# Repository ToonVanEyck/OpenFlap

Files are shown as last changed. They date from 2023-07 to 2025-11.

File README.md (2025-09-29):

# OpenFlap




!!! warning

    🚨 This is still a work in progress. Using the the code and files in this repository to create your own display is not recommended at the moment! 🚨

The OpenFlap project aims to create a open source, affordable split-flap display for the makers and tinkerers of the world.
This repository houses all the required files to build, program and modify your very own split-flap display. 

[**Read the Docs**](https://toonvaneyck.github.io/OpenFlap/)

OpenFlap Module

## Specifications

- 48 Flaps per module.
- 49mm x 70mm Character size.
- Stackable & Chainable.
- Daisy chain communication.
- Per module configuration & calibration.
- HTTP API available.
- Modular design.
- 3D printable parts.

## Design Philosophy

The OpenFlap system is designed to be modular and expandable, using common components and manufacturing techniques such as 3D printing and printed circuit boards.

The OpenFlap system uses DC geared motors instead of traditional stepper motors. This simplifies the mechanical design and reduces the cost of the system. Additionally this reduces the power consumption of the system and allows the split-flap display to rotate faster than the traditionally used stepper motors. 

The OpenFlap system is designed to be as plug and play as possible. The system is able to determine it's own display size, and should only require calibration once.

The OpenFlap system has a web interface that allows local control of the display. The web interface uses a HTTP API to communicate with the display, this API also allows external services to communicate with the display. No authentication or security measures are implemented at the moment.

The OpenFlap system can connect to your local WiFi network or host it's own network.

## I want to ...

[... know more about how the OpenFlap system works.](docs/architecture.md)

[... build my own OpenFlap display.](todo)

[... contribute to the OpenFlap project.](docs/developing.md)

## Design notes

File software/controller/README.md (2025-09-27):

# Controller firmware development with ESP-IDF

To get started, make sure you have build and opened the `esp-idf` devcontainer in VS-Code.

!!! info
    
    All commands below are to be run from the root of the repository.

!!! note

    You may set the `OPENFLAP_DEFAULT_SSID` and `OPENFLAP_DEFAULT_PASSWORD` environment variables to override the default WiFi SSID and password for the controller. If not set, the controller will default to `default_ssid` and `default_password`.

## Build the firmware

```bash
idf.py -B build/controller -C software/controller build
```

## Flash the firmware

```bash
idf.py -B build/controller -C software/controller flash monitor
```

!!! note 

    The first time you program the controller, you will need to use the UART0 RX/TX pads on the bottom of the board. After the initial programming, you can use the USB port to program and debug the controller.+

## Action Buttons

The VS Code devcontainer contains a toolbar with some useful actions for building and flashing the firmware.

ESP-IDF Action Buttons

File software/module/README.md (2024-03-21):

# Puya Playground

This is a VS-Code devcontainer based development environment for the Puya PY32 family of ARM Cortex M0 microcontrollers. It's based on [IOsetting's work](https://github.com/IOsetting/py32f0-template) but it has been wrapped in a devcontainer and I changed the build system to CMake.

I have tested this setup with [this devkit from aliexpress](https://nl.aliexpress.com/item/1005004959178538.html).

## Getting Started

Connect the devkit as shown in the image below.

devkit

Start the development container

In the development container verify that the debug probe is connected:
```
vscode ➜ /workspace/build $ pyocd list
  #   Probe/Board             Unique ID                                          Target         
------------------------------------------------------------------------------------------------
  0   ARM DAPLink CMSIS-DAP   070000003233d72f083932363836374da5a5a5a597969908   ✖︎ stm32f103rb  
      NUCLEO-F103RB
```

## Building
```
mkdir build
cd build
cmake -DCMAKE_TOOLCHAIN_FILE=puya_toolchain.cmake ..
make
make flash
```

## Debugging
A `launch.json` file is configured to use the debug capabilities of VS-Code

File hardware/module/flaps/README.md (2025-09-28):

# Flaps

This repository contains two methods to create the flaps for the OpenFlap split flap display.
Either you can order them as 0.8mm PCB's or you can 3D print them using a multicolor printer.

## Flap Generator

The Flap generator is a browser based tool which allows you to quickly generate a character set for the OpenFlap display. You can select a font, size and the desired character set. Additionally you can adjust the scale, width and position of each character. The tool allows you to export and import your project file so you can continue your work at a later time.

A default character set is contained within the `defaultFlapSet.json` file. This file is loaded by default within the application. The default file contains the following character set:

```text
 ABCDEFGHIJKLMNOPQRSTUVWXYZ0123456789€$!?.,:/@#&
```

By clicking on the **Generate Files** button, a set of *.svg* files are generated for each flap. Each flap contains a top and bottom layer. The top layer contain the upper part of the character and the bottom layer contains the lower part of the next character flipped vertically. All files are bundled in a *.zip* and downloaded to your computer. The *.svg* files within this *.zip* folder are meant to be used by [gerbolyze](https://github.com/jaseg/gerbolyze) to generate the gerber files for the production of the flaps.

A wrapper script `flaps_to_pcb.sh` is provide witch takes two inputs: the input *.zip* file generated by the browser based flap generator and the output directory where the gerber files will be stored. The script will extract the *.zip* file and run `gerbolyze` on each *.svg* file. The output gerber files will be stored as a *.zip* file in the output directory. 

In a similar way, the script `flaps_to_3d.py` takes the same input *.zip* file and generates a set of *.stl* files for each flap. The output *.stl* files are stored in the output directory.

Click the link to use the [Flap Generator](browser_based_flap_generator/index.html).

## Considerations

When creating a character set, make sure the flaps do not have any part of the character show below a certain distance from the bottom. This is because the bottom of previous flaps are always visible on the display. In the OpenFlap display, it's around 5mm from the bottom of the flap. The default character set uses 8mm to be on the safe side.

## ToDo

- Add support for custom svg glyph upload.

## Known Issues

- It's possible that "holes" in svg paths are "closed" when increasing the thickness of a glyph. This will only become apparent when viewing the gerbers as it does not show up in the generator tool.

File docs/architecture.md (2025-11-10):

# Architecture

The OpenFlap system can be divided into 3 main components:

- The [**OpenFlap Module**](module.md)
- The [**OpenFlap Top Connector**](top_connector.md)
- The [**OpenFlap Controller**](controller.md)

To build an OpenFlap display, you need one OpenFlap Controller for the first column of modules, a Top Connector for all other columns of modules, and some OpenFlap Modules.

This chapter describes how these 3 components works and communicate.

## Display Size restrictions

There are two factors that limit the maximum size of the display:

### 1. The power required to drive all the modules.

The lowest rated connection allows for a maximum current of 15A. At 12V this means that the maximum power that can be delivered to the display is 180W. Each module draws around 1W while moving. This limits the maximum 'safe' display size to around 180 modules. As the modules do not rotate all the time, it is possible to drive larger displays, but this has not been tested.

### 2. The memory required by the controller to keep track of all the modules.

The controller keeps an internal representation of the display in memory. The maximum number of modules which can be controlled a the same time without running out of memory is untested at the moment.

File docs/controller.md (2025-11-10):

# OpenFlap Controller

The controller is a special kind of Top Connector. It is meant to be used for the first column of modules in the display. It's based around the espresif ESP32-S3, a low-cost, microcontroller with integrated WiFi and Bluetooth capabilities. 
The controller is responsible for managing and communicating with the modules over UART, as well presenting a web interface and API to the user. 

OpenFlap Controller Render

The controller must be powered from a 12V power supply using the XT-30 connector. A USB port is provided for programming and debugging.

## Additional Resources

- [Schematic](../hardware/controller/controller-schematic.pdf)
- [Interactive BOM](../hardware/controller/controller-ibom.html)
- [KiCanvas](https://kicanvas.org/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)

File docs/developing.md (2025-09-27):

# Developing

This repository contains everything you need to build and develop the OpenFlap display system. To effectively develop and contribute to the project, it's important that you are familiar with the following technologies:

- VS-Code devcontainers
- ESP-IDF & FreeRTOS
- ARM Bare Metal development
- KiCad & FreeCAD

## Devcontainers 

All firmware development for this project is done using VS-Code devcontainers. The repository contains the following devcontainers:

### 1) esp-idf

This development container is set up for developing the controller firmware. It contains the ESP-IDF framework and all the required tools to build and flash the firmware to the controller.

### 2) puya 

This development container is set up for developing the module firmware. It contains the ARM toolchain and all the required tools to build and flash the firmware to the module.

### 3) ecad-mcad

This development container is used for automating the generation of PCB production files and 3D printing files. It contains KiCad, FreeCAD and all the required tools to generate the production files. Actual development of the PCB's and 3D models is done outside of the devcontainer.

## Repository Structure

This repository contains everything you need to build and develop the OpenFlap display system. The repository is structured as follows:

- `.devcontainer`: Contains the devcontainer definitions for the 3 development containers.
- `docs`: Contains the documentation for the project.
- `hardware`: Contains all the hardware (PCB) designs for the project.
- `software`: Contains all the software for the project.
- `mechanical`: Contains all the mechanical designs for the project.

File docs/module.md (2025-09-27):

# OpenFlap Module

The OpenFlap module is the main component of the OpenFlap system. It consists of number of 3D prints and PCBs sandwiched together to create a display.

OpenFlap Module CAD model

The construction of the module can be described as follows:
A 3D printed 'shell' is sandwiched between two side panel PCBs. A 3D printed bearing is mounted on each of the side panels and the 'flap wheel' is mounted on these bearings. The flap wheel consists of 3D printed core sandwiched between two PCBs. All the flaps rest between these two PCBs. 

Only the left side panel PCB is populated with components. The right side panel PCB is left unpopulated and is used to provide mechanical support. 

!!! note

    In theory, the unpopulated side panel PCB could be replaced with a 3D printed part, this 3D printed part could then also be fused with the 'shell' and on of the 'bearings' greatly simplifying the assembly process and reducing the part count. But it would make the design asymmetrical and I just won't have it...

## Side Panel PCB

Two side panels make up the main structure of the module. The left side panel is populated with components and the right side panel is left unpopulated. The side panel PCB is responsible for the following tasks:

- **Motor Control**: The side panel PCB is responsible for controlling the motor that drives the flaps.
- **Communication**: The side panel PCB is responsible for communicating with the controller and the other modules over UART.
- **Flap Detection**: The side panel PCB is responsible for detecting the position of the flaps.

Each left side panel features a [Puya PY32F003F1](https://download.py32.org/ReferenceManual/en/PY32F003%20Reference%20manual%20v1.1_EN.pdf), this is a low cost 32 bit ARM cortex M0+ microcontroller. 

Three [ITR8307](https://www.everlighteurope.com/custom/files/datasheets/DRX-0000321.pdf) reflective optical sensors are used to detect the position of the flaps. They do this by detecting an [incremental encoder](https://en.wikipedia.org/wiki/Incremental_encoder) pattern on the flap wheel. 

The motor is driven by a [L9110S](https://www.lcsc.com/datasheet/lcsc_datasheet_2203301130_LANKE-L9110S_C2984833.pdf) motor driver. PWM is used to modulate the speed of the motor. 

2x7 Pin headers sit at the top and bottom of the PCB to connect the side panel to the other modules. One pin in the bottom header is always pulled low by the next module below it. When the module is the last in the chain, this pin is pulled high by a pull-up resistor. This way the module can determine if it is the last in a column.

OpenFlap Side Panel Render

!!! note

    There is a dependency between the encoder pattern and the position of the IR sensors. The encoder pattern is designed with 48 flaps in mind, this determines the IR sensors placement. If you want to change the number of flaps, you will have to change the encoder pattern and the position of the IR sensors.

### Additional Resources

- [Schematic](../hardware/module/side_panel/side_panel-schematic.pdf)
- [Interactive BOM](../hardware/module/side_panel/side_panel-ibom.html)
- [KiCanvas](https://kicanvas.org/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)

## Encoder Wheels PCB

Two encoder wheel PCB sandwiches the 3D printed "core" of the module. The encoder wheels holds all the flaps and allows the the side panel to track it's rotation.

Each encoder wheel has an A & B side. On the A side, the encoder pattern is offset 4.5° relative to the flap holes. On the B side this offset is 3.75°. This allows you tho switch the side in case the flaps are rotating to far / not far enough.

OpenFlap Encoder Wheels Render

## Flaps

Initially the flaps were designed to be PCB's. But due to the increased accessibility of multicolor 3D printers, the flaps can now also be 3D printed. 

A software tool to generate a custom flap set is included in this repository. As well as script to generate the gerber files or STL files for the flaps. ( TODO: Add link to the tool )

Flap Dimensions

## Shell 

The shell is designed to be 3D printed. Its features include:

- **Mounting holes**: The shell has mounting holes for the side panel PCBs and the top connector.
- **Flap retainer**: The flap retainer, retains the upper flap without covering it up entirely. 
- **Dovetails**: The shell has 2 dovetail cutouts on the back, allowing for flexible mounting options.
- **Ratchet notch**: A notch on the inside of the shell prevents the flap wheel from spinning in the wrong direction.

Openflap Shell Ratchet Notch

When the flap wheel spins and finally reaches its setpoint, the motor will spin in reverse for a short pulse. Because the flaps will lock up against the ratchet notch, all modules will end up at the same position height wise. Additionally, this action will take up the backlash in the gearbox, preventing the flaps from sagging.

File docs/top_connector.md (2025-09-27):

# OpenFlap Top Connector

As the name suggests, the Top Connector is placed at the top of each column of modules. The Top Connector routes power and communication signals to the modules in the column. Top Connectors can be connected together using 2x9 IDC ribbon cables, Allowing the display to be daisy chained to any* width.

OpenFlap Top Connector Render

## Functions

- Receive 12V from previous column and pass it to the next column.
- Convert 12V to 5V using a DC-DC converter and supply it to the modules in the column.
- Route UART signal from previous column through to this column and to the next column.
- Reroute UART back to previous column when this is the last column.

Top Connector Diagram

## Additional Resources

- [Schematic](../hardware/top_connector/top_connector-schematic.pdf)
- [Interactive BOM](../hardware/top_connector/top_connector-ibom.html)
- [KiCanvas](https://kicanvas.org/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)

(*) Power consumption and voltage drop over long cables may limit the practical width of the display.

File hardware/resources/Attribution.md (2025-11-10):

Source files for the 3D models used in the hardware design.
Sources may not be the original creators of the models, but the files were found on the following websites.

| File | Source |
| ---- | --- |
|[694106106102.stp (and .wrl)](694106106102.stp) | [INTI-CMNB on github](https://github.com/INTI-CMNB/kibot_variants_arduprog/tree/master/3D) |
|[DC_jack_plug_5.5x2.5.stp](DC_jack_plug_5.5x2.5.stp) | [nomura.kenzi-1 on grabcad](https://grabcad.com/library/dc-jack-plug-5-5x2-5-angle-1) |
|[EVQ-P7J01P.stp](EVQ-P7J01P.stp) | [snapeda](https://www.snapeda.com/parts/EVQ-P7J01P/Panasonic/view-part/) |
|[GA12-N20.stp](GA12-N20.stp) | [vip1990-1 on grabcad](https://grabcad.com/library/ga12-n20-motor-1) |
|[HLE-107-02-L-DV-BE-A-TR.stp](HLE-107-02-L-DV-BE-A-TR.stp) | [samtec](https://www.samtec.com/products/hle-107-02-l-dv-be-a-tr) |
|[HLE-108-02-L-DV-BE-TR.stp](HLE-108-02-L-DV-BE-TR.stp) | [samtec](https://www.samtec.com/products/hle-108-02-l-dv-be-tr) |
|[IDC_1.27mm_2x3.stp](IDC_1.27mm_2x3.stp) | [bakatrouble-1 on grabcad](https://grabcad.com/library/idc-box-header-1-27mm-1) |
|[IDC_1.27mm_2x5.stp](IDC_1.27mm_2x5.stp) | [bakatrouble-1 on grabcad](https://grabcad.com/library/idc-box-header-1-27mm-1) |
|[Right-angle-USB-C-cable.stp](Right-angle-USB-C-cable.stp) | [mike.d-83 on grabcad](https://grabcad.com/library/right-angle-usb-c-to-4-pin-bare-wire-1) |
|[USB-C.stp](USB-C.stp) | [neal.wong-1 on grabcad](https://grabcad.com/library/usb-type-c16pin-vertical-type-1) |
|[54-00286.STEP](54-00286.STEP) | [Digikey](https://www.digikey.be/en/models/16649077) |
|[WS2812-0807.stp](WS2812-0807.stp) | [ilya.kopytov-1 on grabcad](https://grabcad.com/library/ws2812-0807-1) |
|[XT30-STEP](XT30-STEP) | [stuplja-1 on grabcad](https://grabcad.com/library/xt30-male-connector-1) |

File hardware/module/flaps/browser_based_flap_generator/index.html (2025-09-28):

Project Setup

Load Project

Save Project

Font

Variant

Size

Character Set

Type the complete character set you wish to generate in here.

Show Guide Lines

Top Guide

mm

Bottom Guide

mm

Character Y Offset

mm

Generate Files

Flap Properties

Scale

Thickness

X Position

mm

Y Position

mm

# Welcome to the OpenFlap Flap Generator!

This tool allows you to generate a set of SVG files required to produce the flap PCB's.

Additionally, you can tweak each glyph's position and size.

Once the you have downloaded the ZIP file containing all SVG's, you can convert them to gerbers or stl's using the flaps_to_pcb.sh or flaps_to_3d.py utility in this repository.

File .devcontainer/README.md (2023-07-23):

# OpenFlap dev container 

## How to use the devcontainer

[tutorial](https://code.visualstudio.com/docs/devcontainers/tutorial)

- Open this directory in vscode.
- Make sure the `Dev Containers` extension is installed.
- Open the command pallet with `F1` of `Ctrl+Shif+P` and select `Dev Containers: Open Workspace In Container`.
- The devcointainer will build.

## Adding USB devices to the devcontainer

Based on [this stack overflow answer](https://stackoverflow.com/a/66427245).

Use the files in `.devcontainer/utils`.

On your host machine:
```bash
sudo cp .devcontainer/utils/99-docker-tty.rules /etc/udev/rules.d/99-docker-tty.rules
sudo service udev restart
sudo cp .devcontainer/utils/docker_tty.sh /usr/local/bin/docker_tty.sh
```

## Using git in your container

Vscode should automatically forward your git & ssh credentials if your ssh-agent is running. Otherwise [check this](https://code.visualstudio.com/remote/advancedcontainers/sharing-git-credentials).

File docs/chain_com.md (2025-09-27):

# Communication

The communication system between the controller and the modules is a daisy chain system based on UART. The controller sends a message to the first module, the first module processes the message and sends it to the next module. This continues until the last module in the chain has received the message.

## Header

There are 4 action types for message send by the controller to the modules:

| Value | Action | Description |
|---|---|---|
| 0 | read all | Read a property from all modules. |
| 1 | write sequential | Write a different value to different properties of a number of sequential modules. |
| 2 | write all | Write the same value to the property of all modules. |
| 3 | execute / return code | Signal the modules to execute a command and return a return code. |

The action type of the message is defined by the 2 most significant bits in the message header byte. The six least significant bits are used to define the property to read or write. This means that there are 64 possible properties that can be read or written. Each property has a read and a write length, this length can be either static or dynamic. In the case of a dynamic length, the length is passed in the message itself.

These are the currently supported properties:

| Value | Property | Read Size | Write Size | Description |
|---|---|---|---|---|
| 0 | NONE | 0 | 0 | Nothing |
| 1 | Firmware Version  | Dynamic | 0 | Contains the firmware version |
| 2 | Firmware Update | 0 | 130 | Used for performing a firmware update. |
| 3 | Command | 0 | 1 | Write a special command, e.g.: reboot, ... |
| 4 | Module Info | 1 | 0 | Property containing the module type and column end information. |
| 5 | Character Set | Dynamic | Dynamic | The possible characters supported by this module. |
| 6 | Character Index | 1 | 1 | The index of the character displayed in the character set. |
| 7 | Encoder Offset | 1 | 1 | The offset between the encoder 'zero' and the first character in the set. |
| 8 | Color | 2 | 2 | Flap fore- and background colors. |
| 9 | Motion | 4 | 4 | Rotational speed control. |
| 10 | Minimum rotation  | 1 | 1 | The minimum number of flaps that should be rotated when changing characters. |
| 11 | Sensor threshold  | 4 | 4 | Threshold values for the IR encoders. |

## Checksum 

The tree primary message types (read all, write all, write sequential) include some form of single byte checksum. This checksum allows the controller and modules to verify that the message was received correctly. The checksum is calculated by summing all bytes in the message (excluding the checksum byte itself) and taking the least significant byte of the result. The location and number of checksum bytes depends on the message type.

## Execute / Return Code

This is a special action type that is used to signal the modules to execute a command and return a return code. When this action is used, the 6 property bytes are used to communicate the return code. Each module will logically `OR` its return code with the return code in the header. This way the controller can determine if any module in the chain encountered an error.

## Read All 

This action is used to read a property from all modules in the chain.

The controller initiates a read all action by sending a header with the action set to `read all` followed by two counting bytes. Each module will retransmit the header, the counting bytes will be retransmitted as well, but each module will increment the counting bytes by one. Next, the module will transmit the property data, followed by a checksum. Sequential modules will know how much data from previous modules to retransmit based of the counting bytes. The last module will retransmit to the controller, which can use the counting bytes to figure out how many modules are in the chain.

Here is an example of a read all message with a property size of 2 bytes:
Property Read All Static

When a property has a dynamic read size. The module will first transmit the size of the property data (2 bytes), followed by the property data itself. Sequential modules will first read the size of the property data so they know how much data they need to retransmit.

Property Read All Dynamic

Each module append's its own checksum to the end of its data. This checksum includes the header and sum of the two counting bytes of its own index in the chain.

## Write All

This action is used to write the same property value to all modules in the chain. This is useful for applying bulk changes to all modules. E.g: Homing the display or applying a firmware update.

The controller initiates a write all action by sending a header with the action set to `write all` followed by the property data and a checksum byte. The message is terminated with an `execute / return code` header. Each module will retransmit the `write all` header and the property data. Once a module has retransmitted the property data, and determined the checksum to be valid, it will process the data and wait for the `execute / return code` header. Once it has received the header, it will logically `OR` its return code with the header. If the checksum is invalid, the module will not process the data and will return an error code instead.

Property Write All Static

When a property has a dynamic write size. The module will first transmit the size of the property data (2 bytes) before transmitting the property data itself.

Property Write All Dynamic

## Write Sequential

This action is used to write different property values to different modules in the chain.

The controller will send multiple header and data + checksum packets. Typically one for each module. The message is terminated by two sequential `execute / return code` headers. The first `execute / return code` header gets retransmitted by each module imeadiatly and triggers the processing of the received data. The second `execute / return code` header will only be retransmitted after the module has finished processing the data. The combination of these two `execute / return code` headers allow the modules to know when the controller has finished sending data, and it allows the controller to know when the modules have finished processing the data.

The `NONE` property can be used to skip a module in the chain. This can be useful when you want to write a property to a specific module in the chain.

Dynamic and static property sizes can be mixed in together in a single message. But typically the controller will stick to one property at a time.

Property Write Sequential

## Examples (Outdated, does not contain CS)

The character property is a good example to show the 3 different action types. The character property has a static read and write size of 1 byte. For this example let's assume the character property id is `5` or `0b000101`.

Our headers would look like this:

| Action | Action (bin) | Property (bin) | Header (bin) | Header (hex) |
|---|---|---|---|---|
| read_all  | 0b01000000 | 0b000101 | 0b01000101 | **0x45** |
| write_seq | 0b10000000 | 0b000101 | 0b10000101 | **0x85** |
| write_all | 0b11000000 | 0b000101 | 0b11000101 | **0xC5** |

The character property will return a number between 0 and 47. This number is the index of the character in the character set. For this example let's assume the character set starts like this `_ABCDEFGHIJKLMNOPQRSTUVWXYZ`. So when the character property is set to `0` the character displayed will be `_`, when the character property is set to `1` the character displayed will be `A`, when the character property is set to `2` the character displayed will be `B`, etc.

**We will start by reading the character property from all modules in the chain:**

Example Read All

We can see the controller transmit the read all header `0x45` followed by the counting bytes `0x00 0x00`.
We receive the header `0x45` followed by the counting bytes `0x05 0x00`, followed by 5 bytes of data. The controller can determine that there are 5 modules in the chain by looking at the counting bytes. The data `0x08 0x05 0x0C 0x0C 0x0F` corresponds to the characters `HELLO` in the character map. 

**Let's finish that message:**

We will write `WORLD` to the modules. This corresponds to the character indexes `0x17 0x0F 0x12 0x0C 0x04`. This will require some sequential write messages. We will use the header `0x85` for this.

Example Write Seq

We can see 5 header and data packets being transmitted by the controller followed by an ACK byte. On the receiving site we only see the ACK byte being received, this is because every module 'takes' one message and retransmits the remaining messages. By the message return to the controller, only the ACK remains.

**Finally we clear the display:**

We will write the character index `0x00` to all modules in the chain. We will use the header `0xC5` for this.

Example Write All

We see the header, followed by the data, followed by the ACK byte transmitted by the controller. The exact same data passes through all modules and is received by the controller.

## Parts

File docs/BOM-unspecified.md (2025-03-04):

List of miscellaneous components required for the project. This file will be cleaned up and organized later.

## Module:
- [60 RPM 12V GA12-N20 DC Gear Motor](http://aliexpress.com/item/33022320164.html)
- [3mm motor coupler](https://aliexpress.com/item/4000342135388.html)
- [M2.6 x 8mm screws](https://aliexpress.com/item/1005003094076706.html)

## Top Connector:
- [2x8 Female 2.54mm Low Profile Bottom Entry Header Socket](https://aliexpress.com/item/3256803077112247.html)
- [2x8 2.54mm idc Connector](https://aliexpress.com/item/2255801071215566.html)
- [16 PIN Ribbon Cable](https://aliexpress.com/item/2251832811689611.html)

## Controller:
- [Optional OLED Display](https://aliexpress.com/item/2251832607894397.html)
- [2x3 & 2x5 1.27mm idc Socket](https://aliexpress.com/item/3256805806476804.html)

## Programmers:
- ESP-PROG
- SWD Programmer

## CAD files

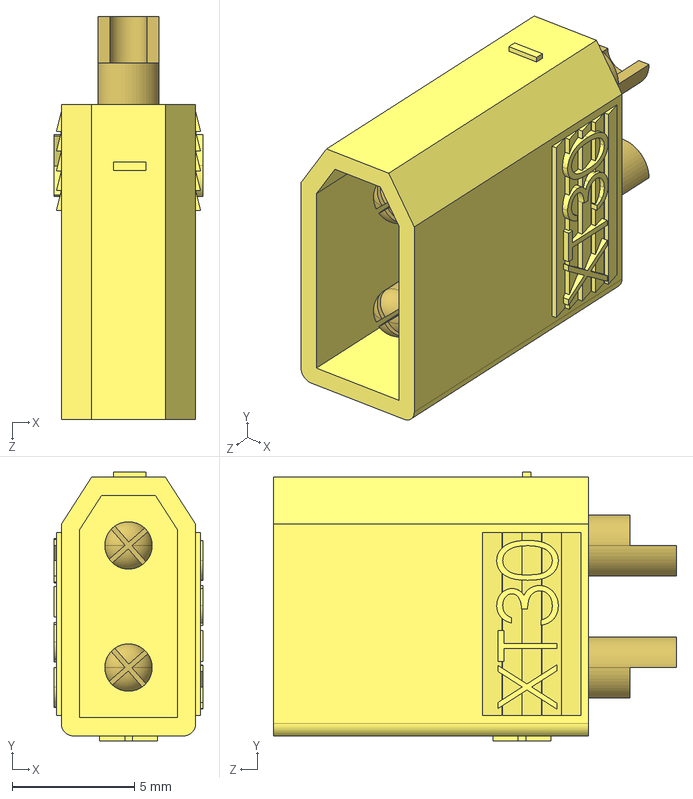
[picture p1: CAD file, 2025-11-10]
hardware/resources/XT30-M.STEP
6.10 x 11.0 x 16.5 mm

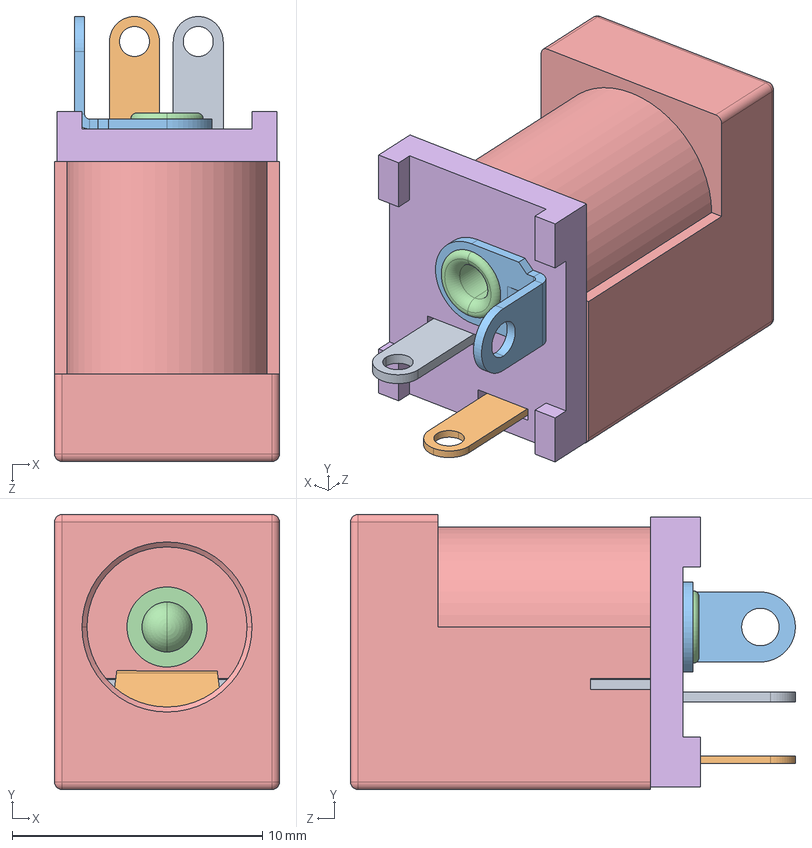
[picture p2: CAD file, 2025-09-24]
hardware/resources/54-00286.STEP
9.00 x 11.0 x 17.8 mm
54-00286_switch
54-00286_spring
54-00286_pin tab
54-00286_pin
54-00286_Insulator
54-00286_Insulator2

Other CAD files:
mechanical/openflap_cad_model.FCStd
hardware/resources/EVQ-P7J01P.stp
hardware/resources/DC_jack_plug_5.5x2.5.stp
hardware/resources/Right-angle-USB-C-cable.stp
hardware/resources/USB-C.stp
hardware/resources/WS2812-0807.stp
hardware/resources/HLE-107-02-L-DV-BE-A-TR.stp
hardware/resources/HLE-108-02-L-DV-BE-TR.stp
hardware/resources/IDC_1.27mm_2x5.stp
hardware/resources/IDC_1.27mm_2x3.stp
hardware/resources/GA12-N20.stp
hardware/resources/694106106102.stp

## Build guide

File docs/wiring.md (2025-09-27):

## Wiring, signaling and power distribution

The system is wired by connecting the top connectors together with a ribbon cable. The first top connector is connected to the OpenFlap Controller. The OpenFlap Modules can be stacked on top of each other and connected to a top connector.

The top connectors and modules a equipped with a sensor witch allows them to detect if they are connected to another module or top connector. This allows the system to determine the size of the display and simplifies the wiring process.

The image below show the signal path from the OpenFlap Controller through the OpenFlap Modules and back:

OpenFlap Signal Path

The controller can be provided with 12V DC power through a barrel jack. This 12V is passed on to the top connectors and modules through the ribbon cable. The top connectors have a voltage regulator that converts the 12V to 5V. This 5V supply is shared by all the modules connected below the top connector.

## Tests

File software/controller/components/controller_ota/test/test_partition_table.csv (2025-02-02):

# Name | Type | SubType | Offset | Size | Flags
nvs | data | nvs | 0x009000 | 16K
otadata | data | ota |  | 8K
phy_init | data | phy |  | 4K
ota_0 | app | ota_0 |  | 4M
ota_1 | app | ota_1 |  | 4M
flash_test | data | fat |  | 100K

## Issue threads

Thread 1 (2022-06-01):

Optimizing for Columns instead of Rows?

graham768, 2022-06-01:
Hey ToonVanEyck,

First of all, I love the work you've done. I think I stumbled onto this project fairly early considering the commit dates and the time stamps on your schematics, but you're really blowing the other "competition" out of the water by making these modules so compact and interchangeable.

With the interchangeability though, I was wondering why you optimized the design for columns. If I'm understanding correctly each column has to have its own top-con board, so if I made a board with 10 modules in a row I'd need 10 top-con boards? Whereas if I made a single column of 10 modules stacked tall, I'd only need a single top-con for the whole system? I would expect most users to have more modules in a row than a column as they write phrases. Let me know if I've misunderstood anything here!

ToonVanEyck, 2022-06-01:
Hey Graham,

Thanks for your intrest in the project.

Each module has two PCB side panels, only one of those PCB's (the left one) has any components on it. The other PCB is the just a structural part. When stacking the modules we can use the headers as implemented in the current design. If we would want to connect them left to right we would need to use a cable or other pcb to connect the left PCB of the first module with the left PCB of the next PCB. This seems like a more complex solution.

Additionally, I wanted the display to be easy to disassemble in the field. It's important to be able to quickly replace one broken module from anywhere in the display. The the top and bottom of the side panel PCB's are rounded. (This is done to reduces the inter-line distance of the display.) Once the modules are stacked and placed in a display, it is impossible to remove a single module or an entire row from a display. It's only possible to remove an entire column from the display, and then break apart that column to replace a broken module.

Because we already have all the connections available on the topmost modules of each column it seemed logical to add a board to facilitate wiring them together.

NOTE: It's entirely possible to wire multiple modules in a row without the use of the top-con boards. (An external 5V supply is required.) The top-con just simplify this greatly.

I agree that horizontal stacking would be more favourable for most users. But the vertical stacking and interconnection was just more practical to implement.  The top-con board allows the horizontal connections to be made with a simple flat-cable to simplify the wiring.

Closed 2022-06-01.

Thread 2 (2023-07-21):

Uploading Flaps Gerbers to JLCPCB

joelhauxwell, 2023-07-21:
Hey ToonVanEyck,

I know the project landing page for this warns against building anything just yet but i would really like to build some of your amazing modules.

I have tried to upload one of the flap gerber zips to JLCPCB but there seems to be an issue with the file.  It opens in the Gerber Preview pane with errors:

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

And in the main order page, the size isn't detected:

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

I could enter the dims manually and select the option for 'confirm production file' -  did you also have to do this?

If you think that me embarking on this project is a terrible idea then please let me know!

Thanks,

Joel.

ToonVanEyck, 2023-07-21:
Hi Joel, JLC pcb seems to have these issues when the Gerber files don't contain anything on the copper layers of the Gerbers. Please let me check if all the latest Gerbers are on GitHub. I will try to update them this weekend. I will also try to write a small manual this weekend.

ToonVanEyck, 2023-07-22:
Hi Joel,

I updated all production files as well as the README. The readme now includes all additional parts you will need as well as all the tools required.
You will also find some additional info for ordering the flaps and encoder wheels on JLCPCB in the readme.
If you have any more questions/issues, don't hesitate to ask them through GitHub issues.

Regards,
Toon

Closed 2023-07-22.

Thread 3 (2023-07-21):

Fusion 360 Links Unauthorized

joelhauxwell, 2023-07-21:
Hey ToonVanEyck,

I can't see the Encoder PCB in the production gerber files and using the Eagle link results in an error -

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

Please could you upload the production files for the encoder wheels when you get a chance?

Thanks,

Joel.

ToonVanEyck, 2023-07-22:
I have removed the links in favour of eagle .sch and .brd files

Closed 2023-07-22.

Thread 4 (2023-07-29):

Alternative for optical sensor

joelhauxwell, 2023-07-29:
Hey,

The optical sensor in the BOM is out of stock at LCSC without a date.

This looks like an appropriate alternative - https://www.lcsc.com/product-detail/Reflective-Optical-Interrupters_Everlight-Elec-ITR8307-S17-TR8-B_C81632.html

What you do think?

Thanks,

Joel.

ToonVanEyck, 2023-07-29:
Seems like it should work. It's cheaper too, so good catch!

Closed 2023-07-29.

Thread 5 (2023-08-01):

[DISCUSSION] Support for multi-width & multi-format displays

sashahilton00, 2023-08-01:
Hi,

I was wondering if there are any plans to support larger displays, both in terms of number of modules, but also in terms of modules of differing width, such as:

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

I have a few thoughts on how one might do this, and might prototype a little, but wanted to check if there is already a WIP on this front:

- Looking at the designs, I'm slightly concerned that if one connected a couple of hundred modules together, that there may be concerns around power draw, possibly necessitating a seperate header (unpopulated by default) for power on each module, which could be used instead of the power from the 16 pin connector for powering the PIC/motor.
- For the multi width side of things, the simplest way in my mind, is to say that the standard module is 1 unit wide, then allow for multiples of the standard unit to be used, to keep the grid type web UI simple, and retain the neat auto discovery functionality.
- Each unit would then store it's size (eg. unit width: 3) in the MCU, and to allow the columnar communication system to continue to work, one would have a simple bridging board that linked the modules above and below an extended width module, with a stored unit length of zero. In this way, a module that detected a module connected below it (ie. column end = false), where that module had a unit width of 0, would allow it to determine that it was sitting on top of a module with a unit length > 1, and be displayed accordingly in the UI. This would probably also require a minor modification to add a lip to the top and bottom casing that would allow modules to snap into to retain their position.

ToonVanEyck, 2023-08-02:
Hi,

Interesting!

I currently do not plan on developing wider modules. I think you are on the right track. E.g.: A 3 wide module should contain 1 PCB with microcontroller, motor, etc... Configured with a `module_width = 3`. And 2 PCBs which just pass through the data signals. These 2 passthrough PCBs should also detect if they are at the end of a column and reroute the data accordingly. I don't think they would require a `module_width = 0`, they don't require a microcontroller. The OpenFlap Controller should be able to calculate the date order in order to "skip" the passthrough PCBs.

Regarding the power usage:
I don't know the power draw at the moment, but the column height will be the limiting factor here. For multiple rows it's trivial to create a customized cable that powers different columns from different supplies. I have ordered materials to build 30 modules, this will allow me to profile the power usage of a somewhat larger display.

I also had the idea for different kinds of modules, e.g.: 7-segment, 16-segment, dotmatrix, nixie tube,...

Regards,
Toon

sashahilton00, 2023-08-02:
I hadn't even thought about the possibility of different types of displays, but that would be very neat. The `module_width = 0` concept was more to account for the fact that columns may not be right next to each other, but spaced out, eg:

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

i.e. the software may think that a module with `module_width = 1` is above/below a module with `module_width = 3`, where in fact it is off to the side, after the 3 width module. However, looking at layouts such as the one above, I'm not sure this is an issue worth facing right now, as I have yet to find many module layouts where the widths of the modules are mixed for a single column. For any edge cases, it's probably easier + cheaper to handle this in the controller as you mention.

It's been a little while since I've played around in autocad/eagle, but will try to pick it back up and make some proof of concepts for wider modules/bridging boards.

In the meantime, I'll rename this issue as a discussion thread for multi width/format displays and leave it open for future discussion/thoughts.

Closed 2024-05-20.

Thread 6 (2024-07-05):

Project status

hamishfagg, 2024-07-05:
Hi there,

First of all, I love this approach to making a split flap display. Its the best I've seen of all the open attempts at this.

The readme warns against making one of these at the moment - what are the hurdles preventing this from being ready to build? Are there any major issues still to work out?

P.S. Have you tried to make a PCB panel with all of the flaps for one display on it? Even as low as JLC prices are, I wonder if they could be lower with a panel.

Thanks for posting this great project!

shagadeli, 2024-07-12:
I'm also very excited to build my own but holding up for an update!
Congratulations on this project @ToonVanEyck , looking forward for some news

ToonVanEyck, 2024-07-12:
Thanks for the kind words guys.

This is very much a hobby project going at a hobby project pace. My life is kind of busy at the moment but I'm trying to work on this at least once a week.

At this moment the repo is kind of a mess, so I would recommend not trying to build it at the moment.

1) I need to update the readme.

2) I need to update all the hardware related files. I'm using Fusion 360 witch is cloud based so I need to download the files and put them in the repo manually. I would prefer to use FreeCad and KiCad as they work with local files but I'm not familiar with the software.

3) I need to reimplements the communication protocol and uart driver on the modules as it is not stable and has some bugs which is preventing the OTA updates from working. Once the OTA is stable I would be able to update the firmware of a whole display at once. Which would allow me to develop a bit faster.

4) I have new hardware where I changed from a MOSFET to an H-bridge to drive the motor. This would allow active breaking of the flap wheel. This is something I want to experiment with.

The silk screen has to be the same for all pcb's in a panel so you would need to order at least 48 panels. I did check the pricing at one point and it was cheaper to not panelized. But pricing often changes at JLC so I don't know if that is still the case.

Regards,
Toon

shagadeli, 2024-07-12:
Great to hear back from you!

I'll be following this so I can order the hardware as soon as you update.
Thanks!

Closed 2024-07-23.

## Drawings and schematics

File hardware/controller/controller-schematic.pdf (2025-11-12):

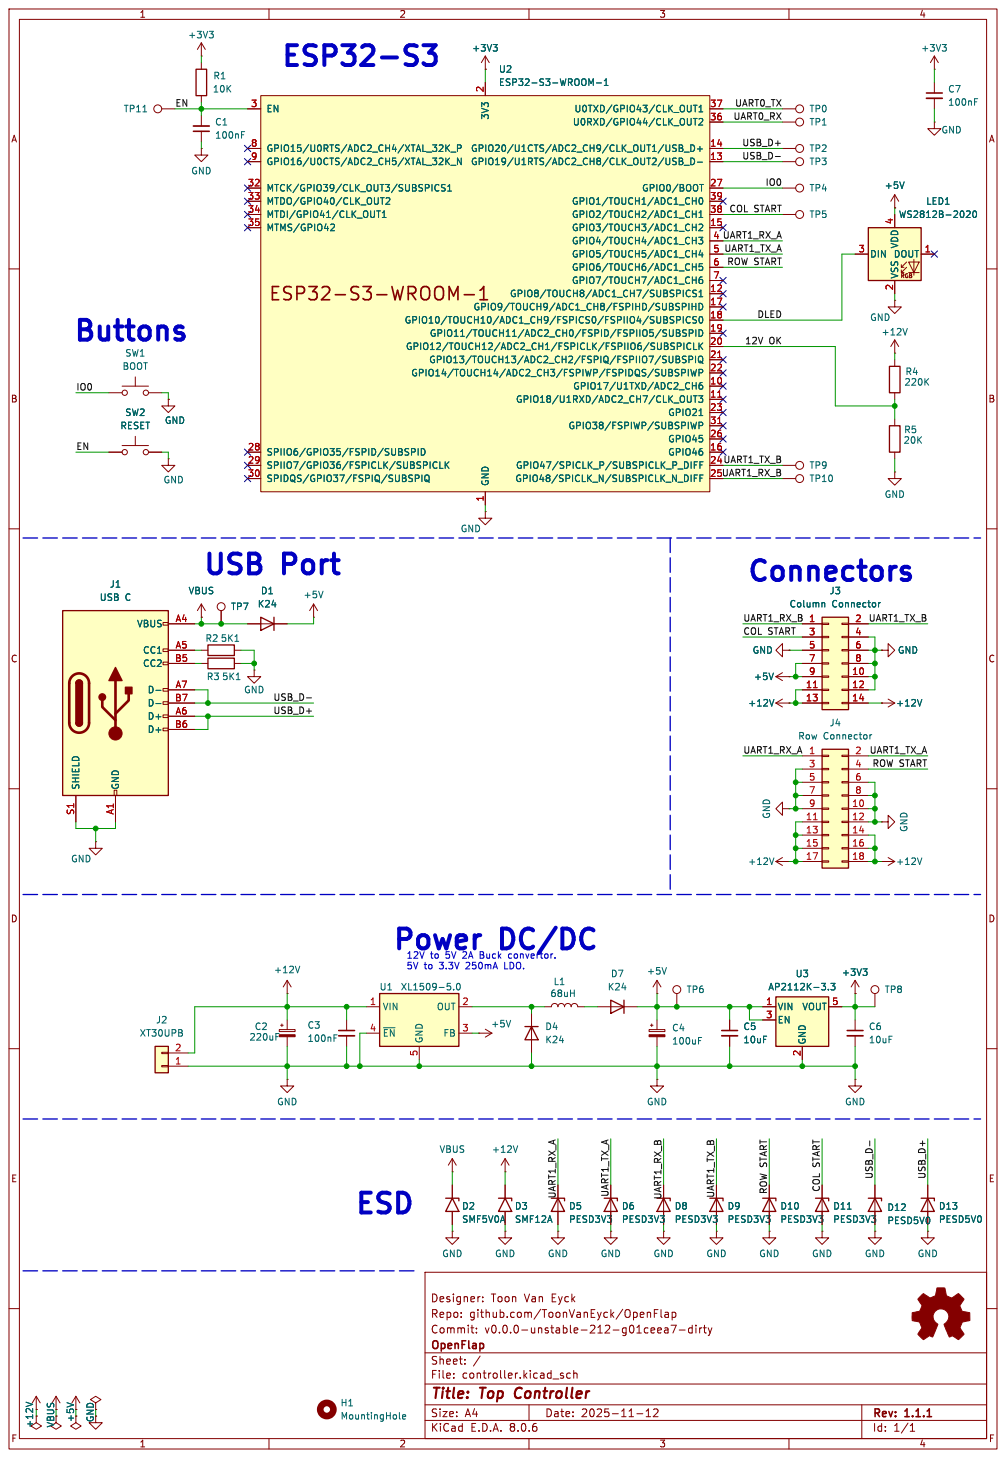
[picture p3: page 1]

2 GPIO12/TOUCH12/ADC2_CH1/FSPICLK/FSPIIO6/SUBSPICLK 20 GPIO13/TOUCH13/ADC2_CH2/FSPIQ/FSPIIO7/SUBSPIQ 21 GPIO14/TOUCH14/ADC2_CH3/FSPIWP/FSPIDQS/SUBSPIWP 22 GPIO21 23 GPIO47/SPICLK_P/SUBSPICLK_P_DIFF 24 GPIO48/SPICLK_N/SUBSPICLK_N_DIFF 25 GPIO45 26 GPIO0/BOOT 27 SPIIO6/GPIO35/FSPID/SUBSPID 28 SPIIO7/GPIO36/FSPICLK/SUBSPICLK 29 EN 3 SPIDQS/GPIO37/FSPIQ/SUBSPIQ 30 GPIO38/FSPIWP/SUBSPIWP 31 MTCK/GPIO39/CLK_OUT3/SUBSPICS1 32 MTDO/GPIO40/CLK_OUT2 33 MTDI/GPIO41/CLK_OUT1 34 MTMS/GPIO42 35 U0RXD/GPIO44/CLK_OUT2 36 U0TXD/GPIO43/CLK_OUT1 37 GPIO2/TOUCH2/ADC1_CH1 38 GPIO1/TOUCH1/ADC1_CH0 39 GPIO4/TOUCH4/ADC1_CH3 4 GPIO5/TOUCH5/ADC1_CH4 5 GPIO6/TOUCH6/ADC1_CH5 6 GPIO7/TOUCH7/ADC1_CH6 7 GPIO15/U0RTS/ADC2_CH4/XTAL_32K_P 8 GPIO16/U0CTS/ADC2_CH5/XTAL_32K_N 9 +3V3 SW2 RESET GND +12V VBUS +5V GND

2 GPIO12/TOUCH12/ADC2_CH1/FSPICLK/FSPIIO6/SUBSPICLK 20 GPIO13/TOUCH13/ADC2_CH2/FSPIQ/FSPIIO7/SUBSPIQ 21 GPIO14/TOUCH14/ADC2_CH3/FSPIWP/FSPIDQS/SUBSPIWP 22 GPIO21 23 GPIO47/SPICLK_P/SUBSPICLK_P_DIFF 24 GPIO48/SPICLK_N/SUBSPICLK_N_DIFF 25 GPIO45 26 GPIO0/BOOT 27 SPIIO6/GPIO35/FSPID/SUBSPID 28 SPIIO7/GPIO36/FSPICLK/SUBSPICLK 29 EN 3 SPIDQS/GPIO37/FSPIQ/SUBSPIQ 30 GPIO38/FSPIWP/SUBSPIWP 31 MTCK/GPIO39/CLK_OUT3/SUBSPICS1 32 MTDO/GPIO40/CLK_OUT2 33 MTDI/GPIO41/CLK_OUT1 34 MTMS/GPIO42 35 U0RXD/GPIO44/CLK_OUT2 36 U0TXD/GPIO43/CLK_OUT1 37 GPIO2/TOUCH2/ADC1_CH1 38 GPIO1/TOUCH1/ADC1_CH0 39 GPIO4/TOUCH4/ADC1_CH3 4 GPIO5/TOUCH5/ADC1_CH4 5 GPIO6/TOUCH6/ADC1_CH5 6 GPIO7/TOUCH7/ADC1_CH6 7 GPIO15/U0RTS/ADC2_CH4/XTAL_32K_P 8 GPIO16/U0CTS/ADC2_CH5/XTAL_32K_N 9 U2ESP32-S3-WROOM-1

1 GPIO17/U1TXD/ADC2_CH6 10 GPIO18/U1RXD/ADC2_CH7/CLK_OUT3 11 GPIO8/TOUCH8/ADC1_CH7/SUBSPICS1 12 GPIO19/U1RTS/ADC2_CH8/CLK_OUT2/USB_D- 13 GPIO20/U1CTS/ADC2_CH9/CLK_OUT1/USB_D+ 14 GPIO3/TOUCH3/ADC1_CH2 15 GPIO46 16 GPIO9/TOUCH9/ADC1_CH8/FSPIHD/SUBSPIHD 17 GPIO10/TOUCH10/ADC1_CH9/FSPICS0/FSPIIO4/SUBSPICS0 18 GPIO11/TOUCH11/ADC2_CH0/FSPID/FSPIIO5/SUBSPID 19 3V3

12V to 5V 2A Buck convertor. 5V to 3.3V 250mA LDO. Buttons

Repo: github.com/ToonVanEyck/OpenFlap
Id: 1/1 Title: Top Controller File: controller.kicad_sch Sheet: / OpenFlap Commit: v0.0.0-unstable-212-g01ceea7-dirty

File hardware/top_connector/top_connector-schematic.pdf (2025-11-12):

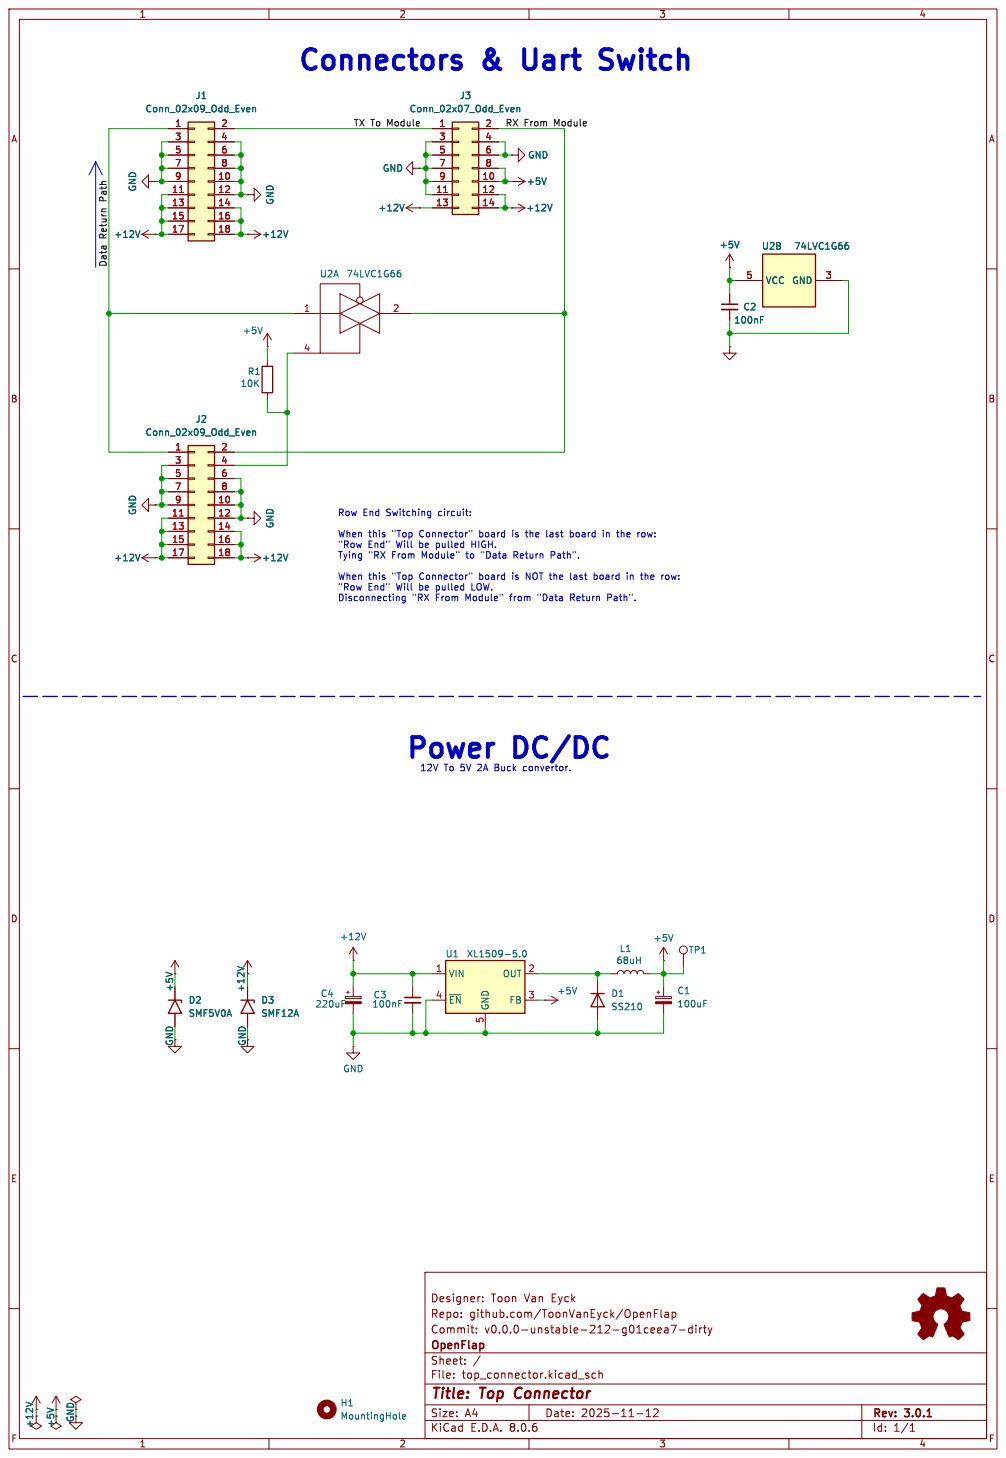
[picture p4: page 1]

Repo: github.com/ToonVanEyck/OpenFlap
Id: 1/1 Title: Top Connector File: top_connector.kicad_sch Sheet: / OpenFlap Commit: v0.0.0-unstable-212-g01ceea7-dirty

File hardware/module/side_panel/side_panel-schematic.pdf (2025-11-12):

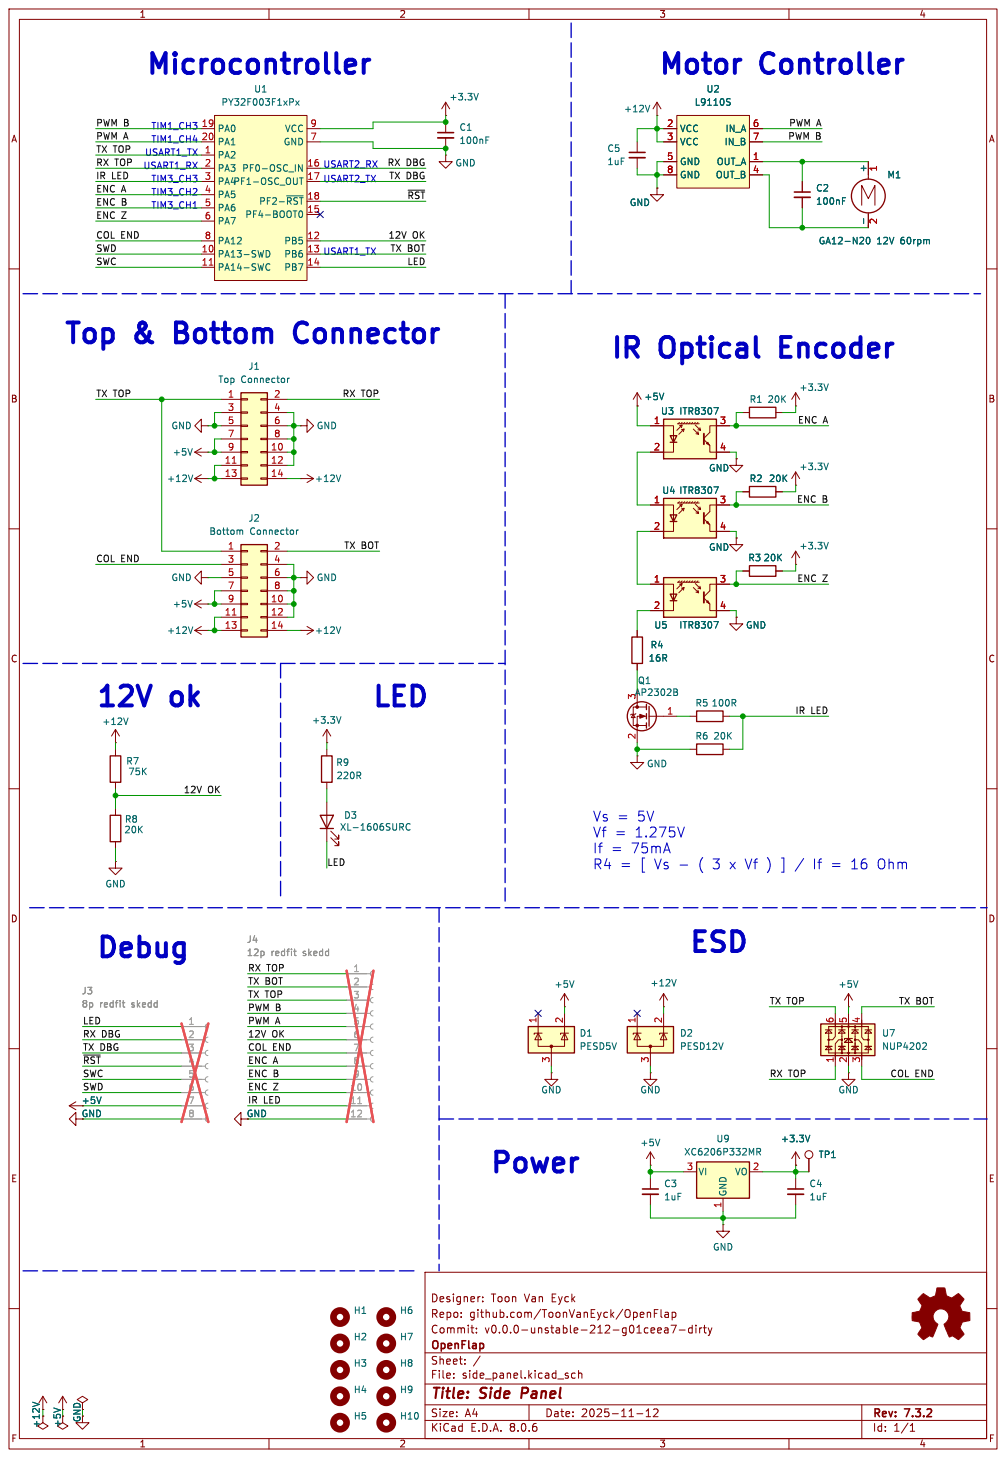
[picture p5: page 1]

12p redfit skedd
PWM A RX TOP
TX BOT COL END
TX TOP
PWM B

Repo: github.com/ToonVanEyck/OpenFlap
Id: 1/1 Title: Side Panel File: side_panel.kicad_sch Sheet: / OpenFlap Commit: v0.0.0-unstable-212-g01ceea7-dirty

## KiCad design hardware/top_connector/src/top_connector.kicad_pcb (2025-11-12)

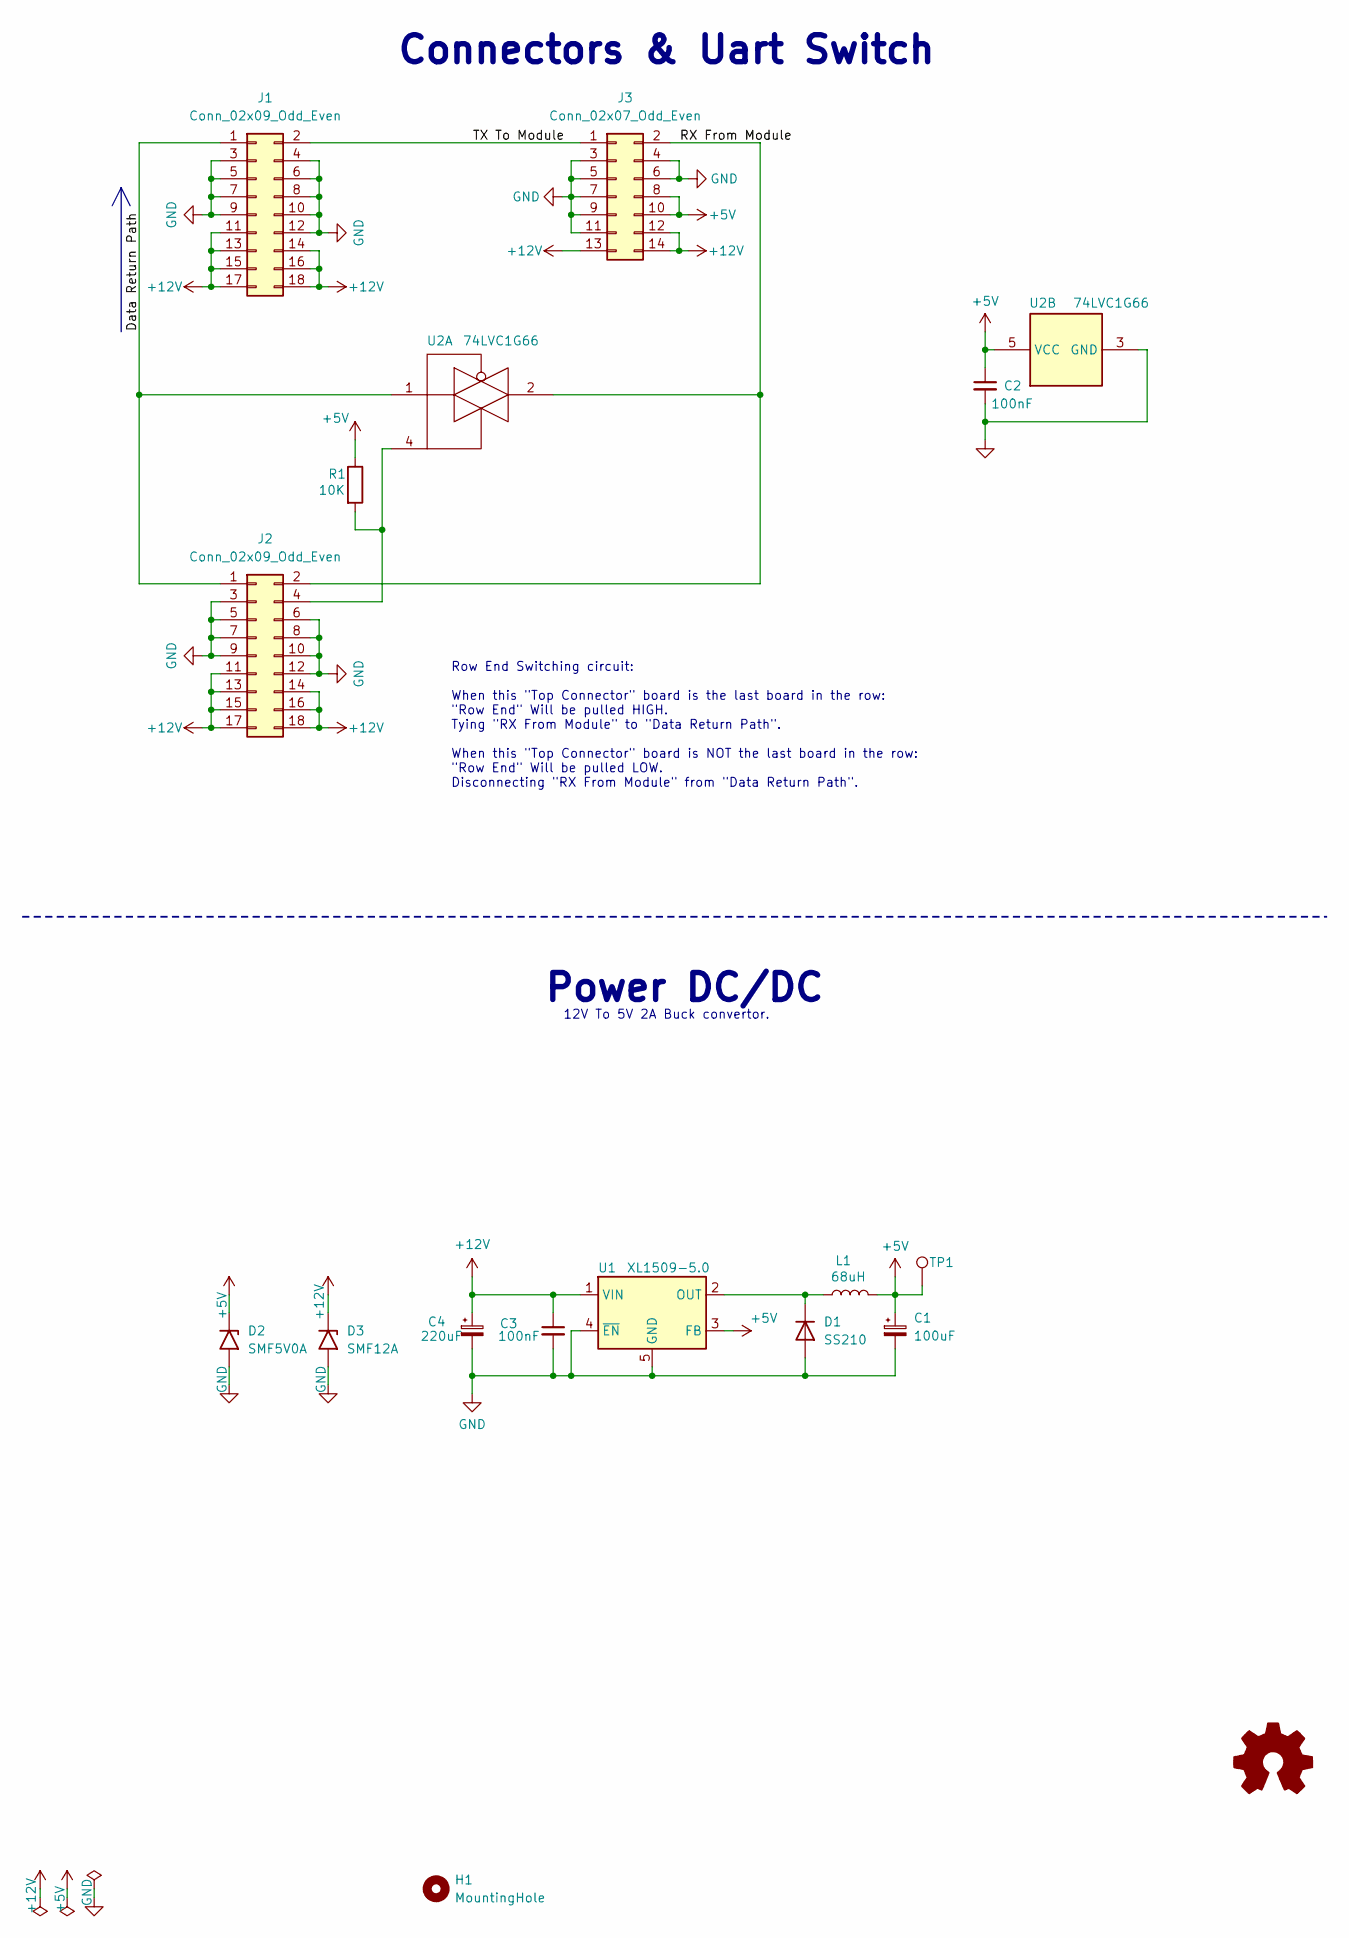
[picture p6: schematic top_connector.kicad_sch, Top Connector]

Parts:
C1: 100uF; CP_EIA-3528-21_Kemet-B; LCSC C16133
C2, C3: 100nF; C_0805_2012Metric
C4: 220uF; CP_Elec_6.3x7.7; LCSC C280399
D1: SS210; D_SMA; LCSC C14996
D2: SMF5V0A; D_SMF
D3: SMF12A; D_SMF
H1: MountingHole; MountingHole_2.7mm_M2.5
J1, J2: Conn_02x09_Odd_Even; IDC-Header_2x09_P2.54mm_Vertical
J3: Conn_02x07_Odd_Even; Samtec_HLE-107-02-xxx-DV-BE-A_2x07_P2.54mm_Horizontal
L1: 68uH; L_Sunlord_SWPA6045S; LCSC C53663
R1: 10K; R_0805_2012Metric
TP1: TestPoint; TestPoint_Pad_D1.5mm
U1: XL1509-5.0; SOIC-8_3.9x4.9mm_P1.27mm; LCSC C61063
U2: 74LVC1G66; SOT-23-5; LCSC C5375974

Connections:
+5V: C1.1, C2.1, D2.1 (A1), J3.8, J3.10, L1.2, R1.1, TP1.1, U1.3 (FB), U2.5 (VCC)
+12V: C3.1, C4.1, D3.1 (A1), J1.11, J1.13, J1.14, J1.15, J1.16, J1.17, J1.18, J2.11, J2.13, J2.14, J2.15, J2.16, J2.17, J2.18, J3.12, J3.13, J3.14, U1.1 (VIN)
/Data Return Path: J1.1, J2.1, U2.1
/RX From Module: J2.2, J3.2, U2.2
/TX To Module: J1.2, J3.1
GND: C1.2, C2.2, C3.2, C4.2, D1.2 (A), D2.2 (A2), D3.2 (A2), J1.3, J1.4, J1.5, J1.6, J1.7, J1.8, J1.9, J1.10, J1.12, J2.3, J2.5, J2.6, J2.7, J2.8, J2.9, J2.10, J2.12, J3.3, J3.4, J3.5, J3.6, J3.7, J3.9, J3.11, U1.4 (~EN), U1.5 (GND), U1.6 (GND), U1.7 (GND), U1.8 (GND), U2.3 (GND)
unnamed: D1.1 (K), L1.1, U1.2 (OUT)
unnamed: J2.4, R1.2, U2.4

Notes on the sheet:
Power DC/DC
12V To 5V 2A Buck convertor.
Row End Switching circuit: When this "Top Connector" board is the last board in the row: "Row End" Will be pulled HIGH. Tying "RX From Module" to "Data Return Path". When this "Top Connector" board is NOT the last board in the row: "Row End" Will be pulled LOW. Disconnecting "RX From Module" from "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
Connectors & Uart Switch

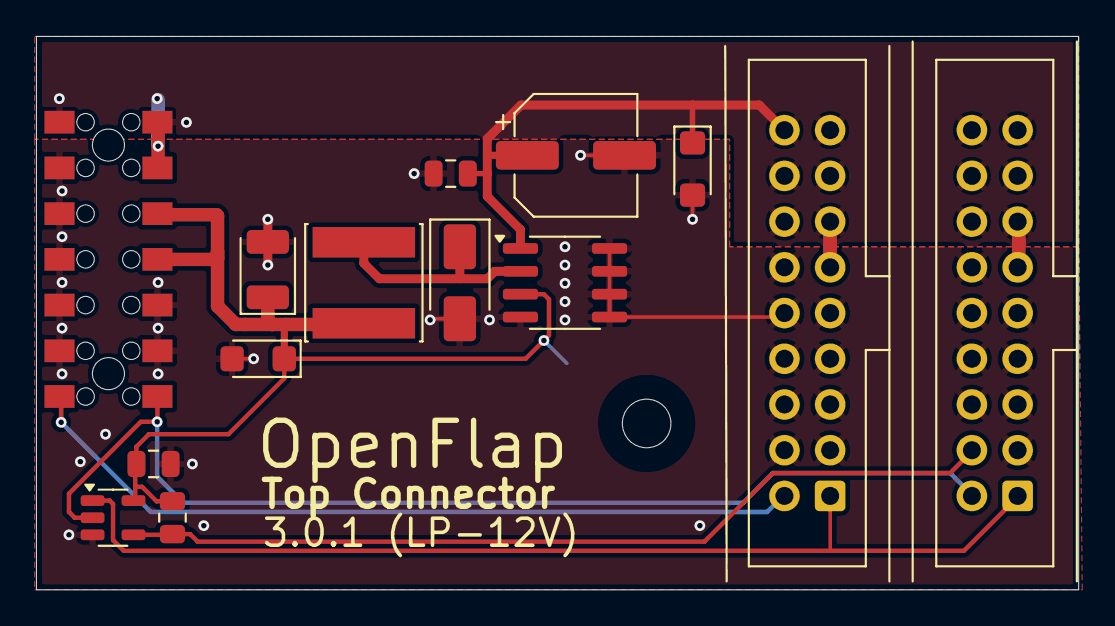
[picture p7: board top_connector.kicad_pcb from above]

Board: 2 copper layers, 57.9 x 30.7 mm, 16 parts (1 on the bottom side), 8 nets.

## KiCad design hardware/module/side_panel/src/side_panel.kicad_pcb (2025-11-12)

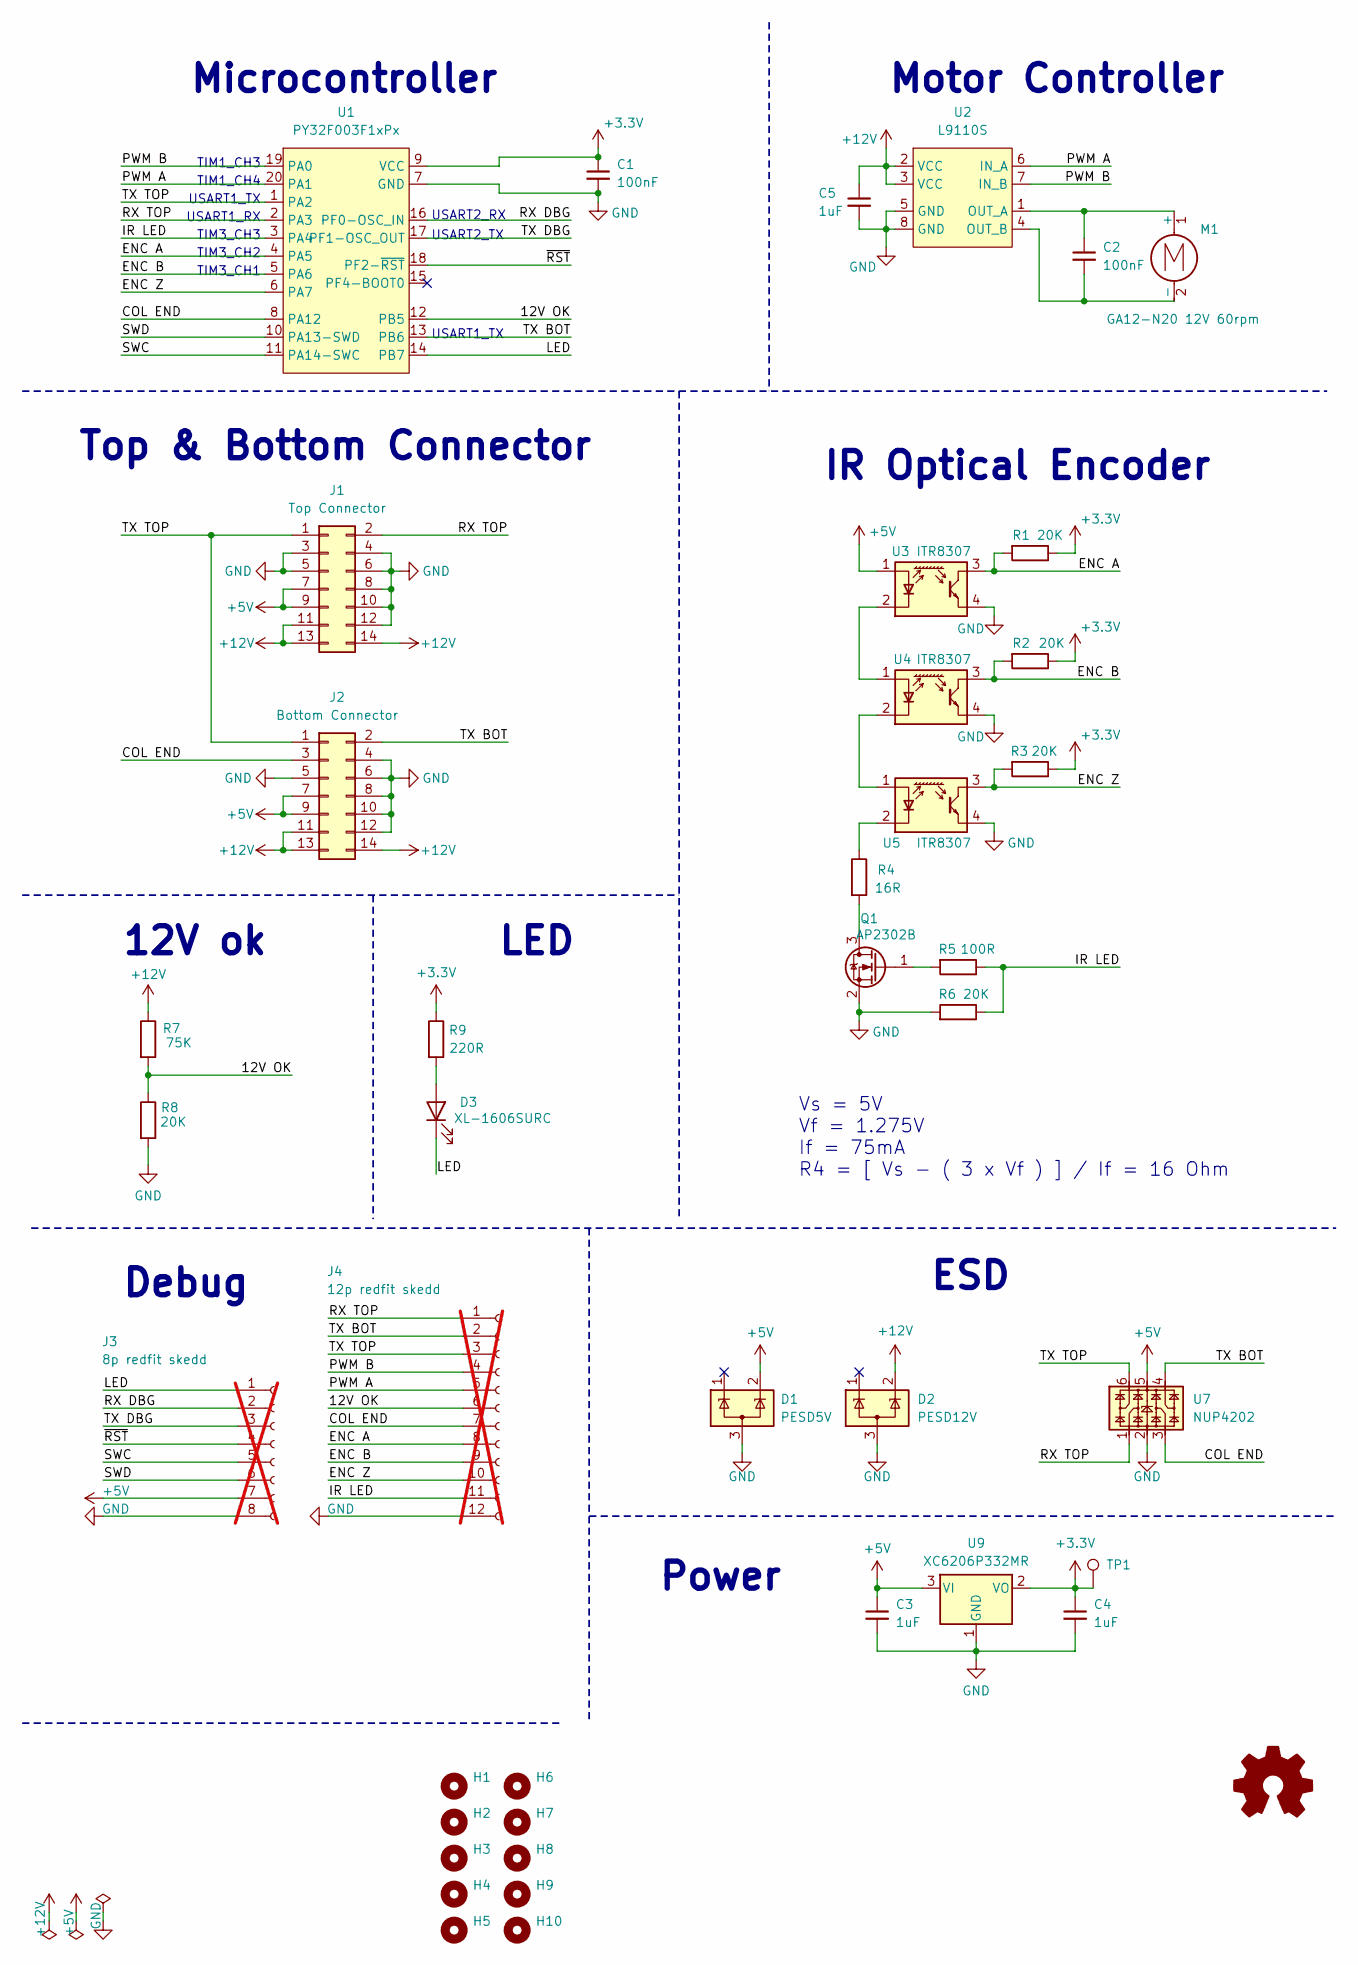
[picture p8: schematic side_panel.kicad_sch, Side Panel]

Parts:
C1, C2: 100nF; C_0805_2012Metric
C3, C4, C5: 1uF; C_0805_2012Metric
D1: PESD5V; SOT-23-3
D2: PESD12V; SOT-23-3
D3: XL-1606SURC; LED_Kingbright_APA1606_1.6x0.6mm_Horizontal; LCSC C965860
H1, H2, H3, H4, H5, H6, H7, H8, H9, H10: MountingHole; MountingHole_2.7mm
J1: Top Connector; PinHeader_2x07_P2.54mm_Horizontal
J2: Bottom Connector; PinSocket_2x07_P2.54mm_Horizontal
J3: 8p redfit skedd; 490107670812; not fitted
J4: 12p redfit skedd; 490107671212; not fitted
M1: GA12-N20 12V 60rpm; GA12-N20 Motor Vertical
Q1: AP2302B; SOT-23; LCSC C406812
R1, R2, R3, R6, R8: 20K; R_0805_2012Metric
R4: 16R; R_0805_2012Metric
R5: 100R; R_0805_2012Metric
R7: 75K; R_0805_2012Metric
R9: 220R; R_0805_2012Metric
TP1: TestPoint; TestPoint_Pad_D1.5mm
U1: PY32F003F1xPx; TSSOP-20_4.4x6.5mm_P0.65mm; LCSC C5379864
U2: L9110S; SOP-8_3.76x4.96mm_P1.27mm; LCSC C2984833
U3, U4, U5: ITR8307; OnSemi_CASE100CY; LCSC C81632
U7: NUP4202; SOT-23-6; LCSC C5199189
U9: XC6206P332MR; SOT-23-3

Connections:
+3.3V: C1.1, C4.1, R1.1, R2.1, R3.1, R9.1, TP1.1, U1.9 (VCC), U9.2 (VO)
+5V: C3.1, D1.2 (K), J1.7, J1.9, J2.7, J2.9, J3.7, U3.1 (A), U7.5, U9.3 (VI)
+12V: C5.1, D2.2 (K), J1.11, J1.13, J1.14, J2.11, J2.13, J2.14, R7.1, U2.2 (VCC), U2.3 (VCC)
/12V OK: J4.6, R7.2, R8.1, U1.12 (PB5)
/COL END: J2.3, J4.7, U1.8 (PA12), U7.3
/ENC A: J4.8, R1.2, U1.4 (PA5), U3.3
/ENC B: J4.9, R2.2, U1.5 (PA6), U4.3
/ENC Z: J4.10, R3.2, U1.6 (PA7), U5.3
/IR LED: J4.11, R5.1, R6.1, U1.3 (PA4)
/LED: D3.1 (K), J3.1, U1.14 (PB7)
/PWM A: J4.5, U1.20 (PA1), U2.6 (IN_A)
/PWM B: J4.4, U1.19 (PA0), U2.7 (IN_B)
/RX DBG: J3.2, U1.16 (PF0-OSC_IN)
/RX TOP: J1.2, J4.1, U1.2 (PA3), U7.1
/SWC: J3.5, U1.11 (PA14-SWC)
/SWD: J3.6, U1.10 (PA13-SWD)
/TX BOT: J2.2, J4.2, U1.13 (PB6), U7.4
/TX DBG: J3.3, U1.17 (PF1-OSC_OUT)
/TX TOP: J1.1, J2.1, J4.3, U1.1 (PA2), U7.6
/~RST: J3.4, U1.18 (PF2-~RST)
GND: C1.2, C3.2, C4.2, C5.2, D1.3 (A), D2.3 (A), J1.3, J1.4, J1.5, J1.6, J1.8, J1.10, J1.12, J2.4, J2.5, J2.6, J2.8, J2.10, J2.12, J3.8, J4.12, Q1.2 (S), R6.2, R8.2, U1.7 (GND), U2.5 (GND), U2.8 (GND), U3.4, U4.4, U5.4, U7.2, U9.1 (GND)
unnamed: D3.2 (A), R9.2
unnamed: C2.1, M1.1 (+), U2.1 (OUT_A)
unnamed: C2.2, M1.2 (-), U2.4 (OUT_B)
unnamed: Q1.3 (D), R4.2
unnamed: Q1.1 (G), R5.2
unnamed: U3.2 (K), U4.1 (A)
unnamed: U4.2 (K), U5.1 (A)
unnamed: R4.1, U5.2 (K)

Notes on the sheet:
USART1_RX
USART1_TX
LED
TIM1_CH3
Top & Bottom Connector
TIM3_CH2
Power
IR Optical Encoder
12V ok
TIM1_CH4
USART2_RX
TIM3_CH3
Vs = 5V Vf = 1.275V If = 75mA R4 = [ Vs - ( 3 x Vf ) ] / If = 16 Ohm
ESD
Motor Controller
Microcontroller
USART2_TX
TIM3_CH1
Debug

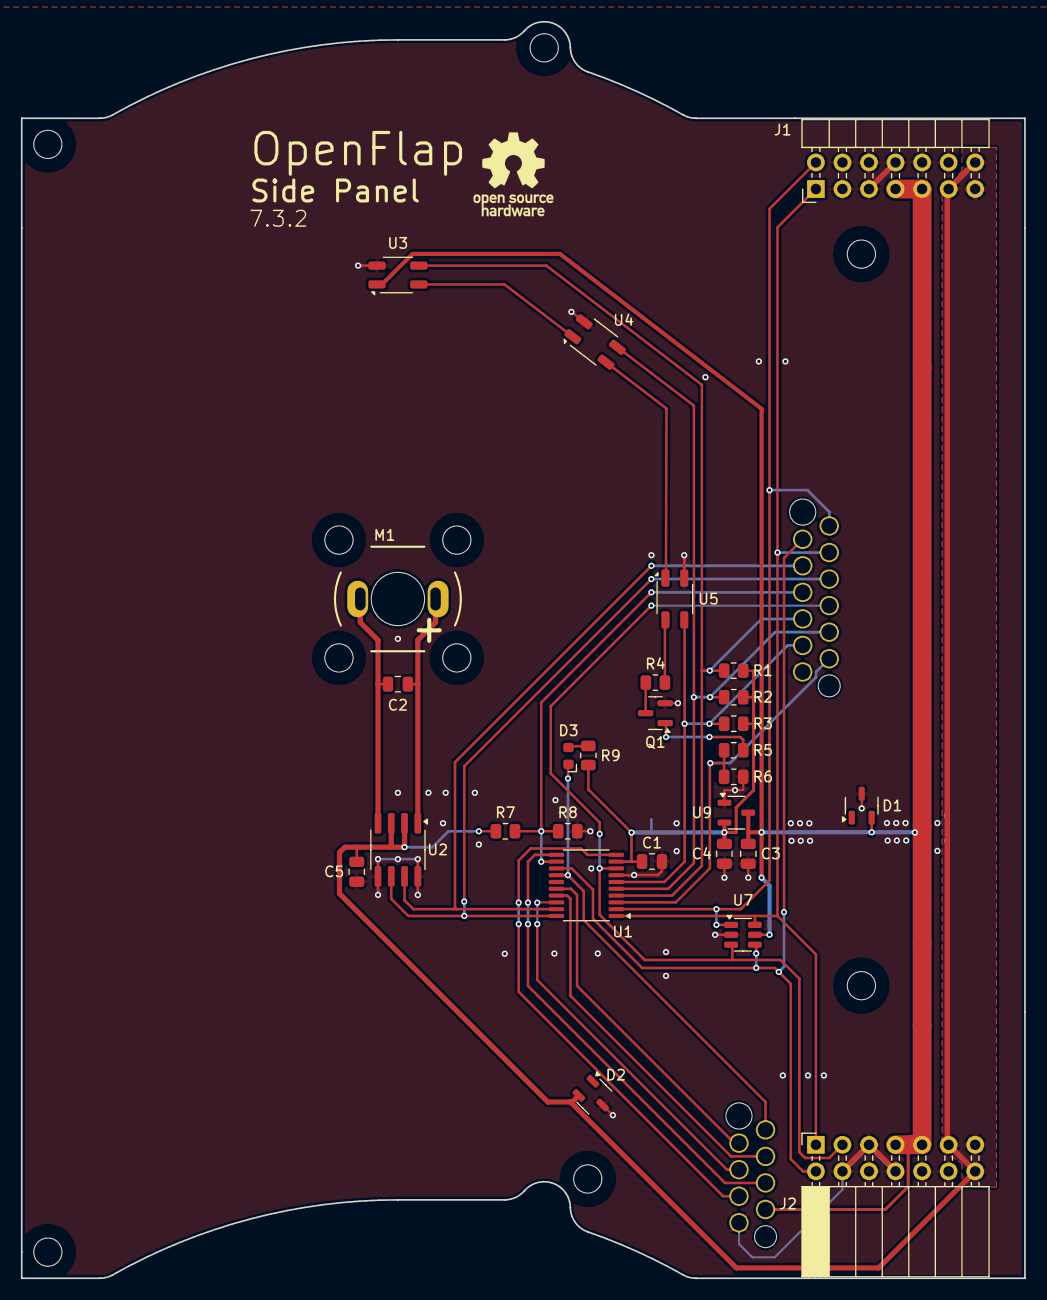
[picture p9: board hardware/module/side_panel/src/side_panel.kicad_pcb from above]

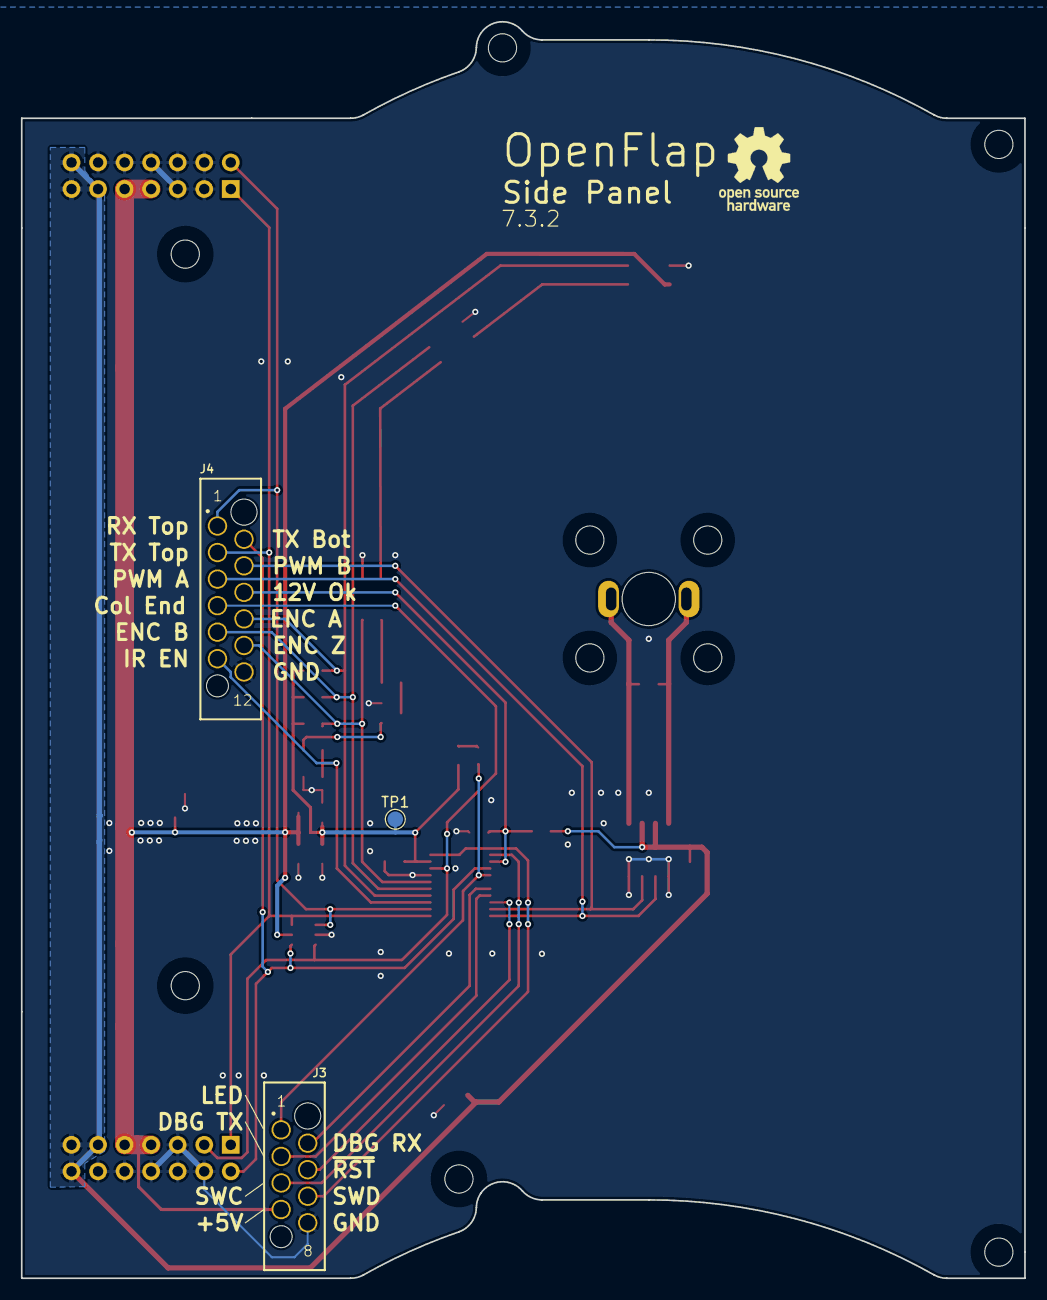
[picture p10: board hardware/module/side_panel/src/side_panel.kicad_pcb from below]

Board: 2 copper layers, 96.0 x 120.2 mm, 43 parts (4 on the bottom side), 29 nets.

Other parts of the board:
OSHW-LOGO-1, OSHW-LOGO-2: OSHW-Logo_7.5x8mm_SilkScreen

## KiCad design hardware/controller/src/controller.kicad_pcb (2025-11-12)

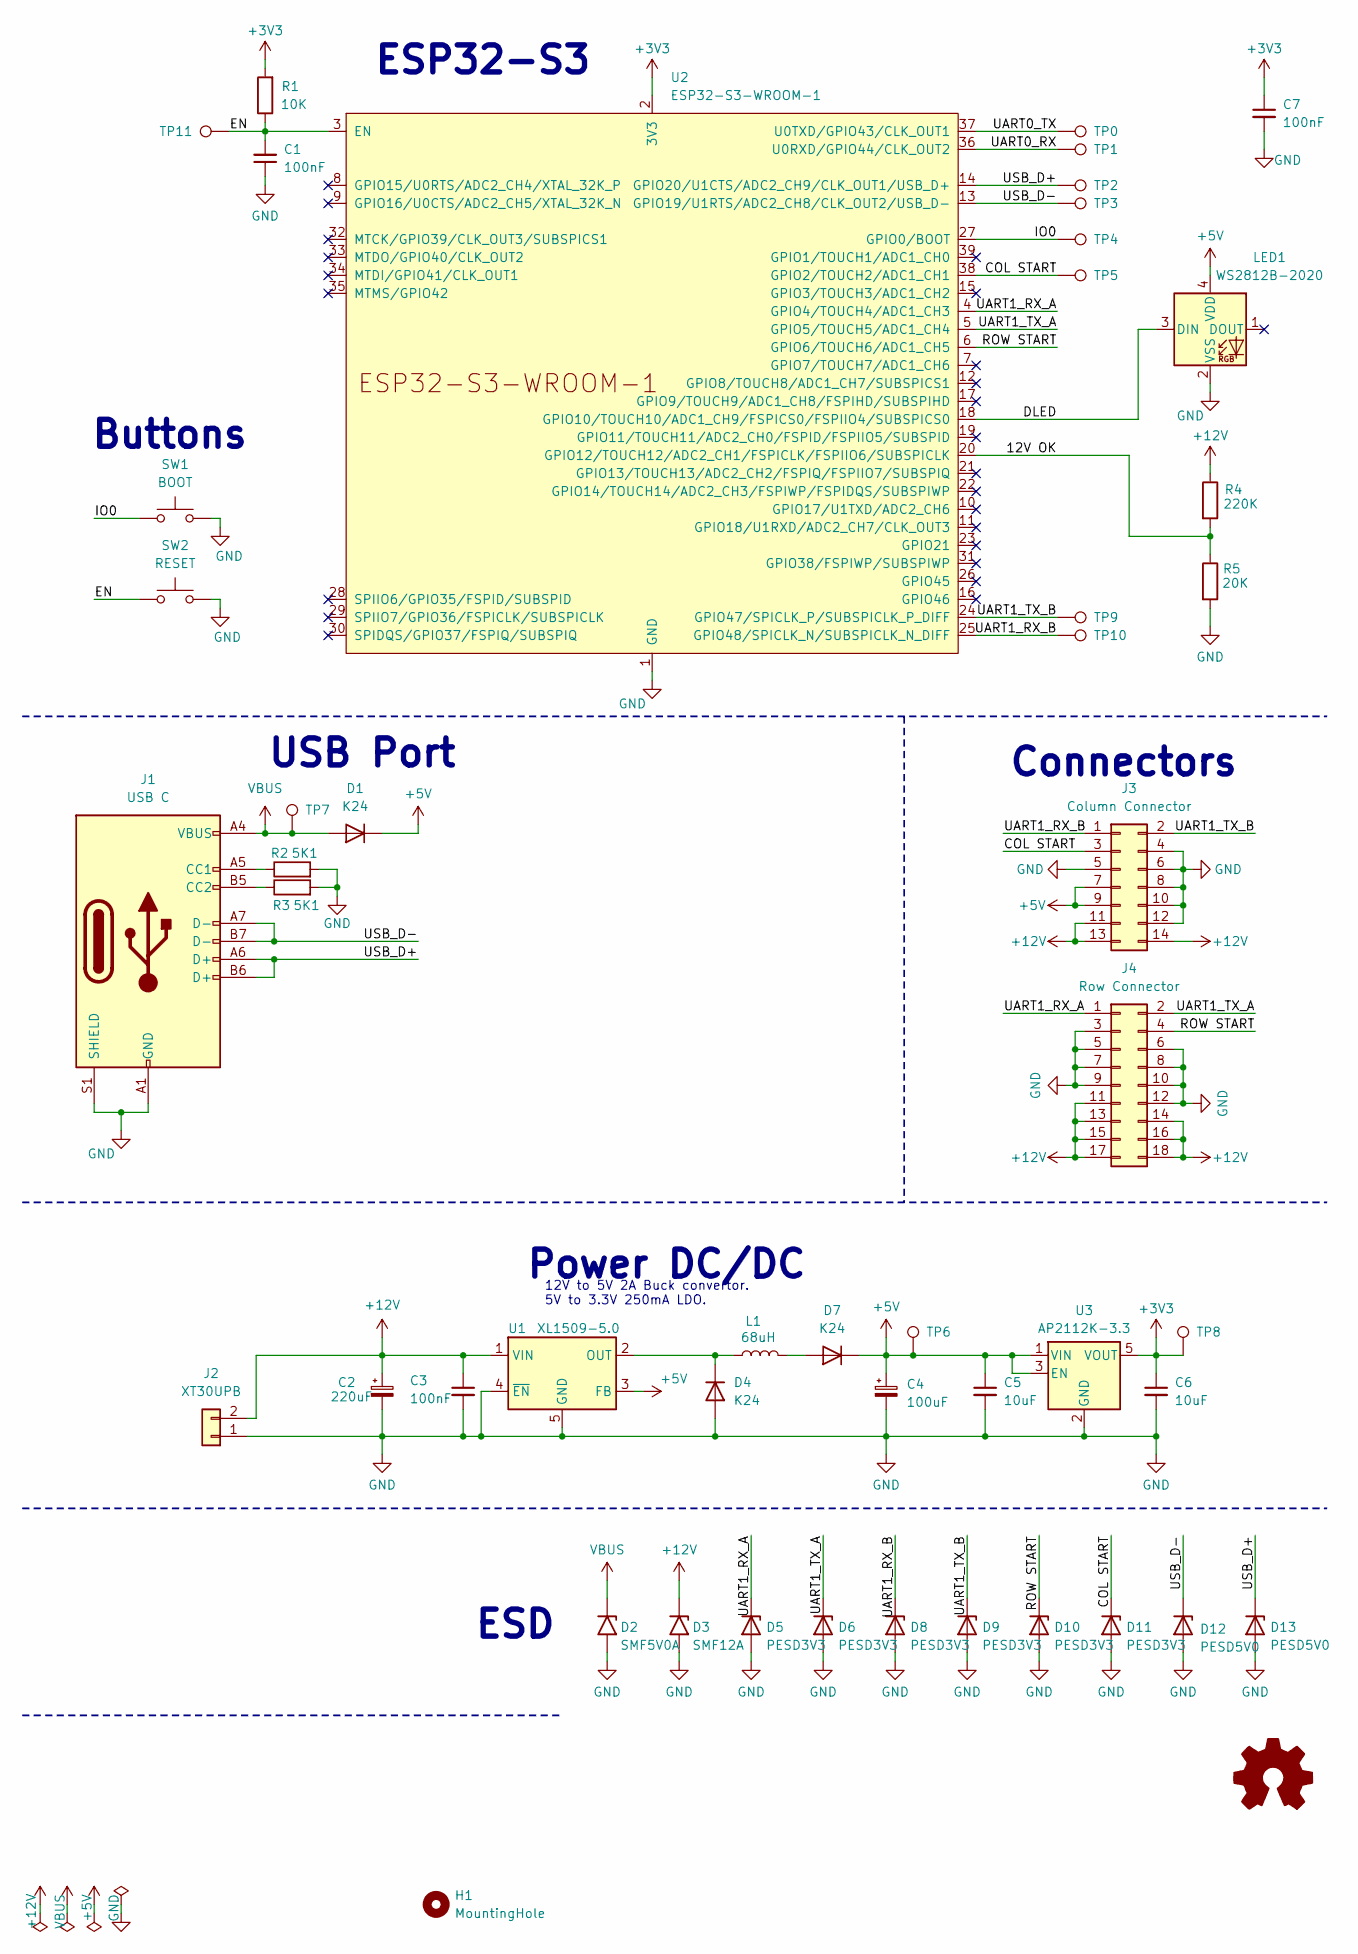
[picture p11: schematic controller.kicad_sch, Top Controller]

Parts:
C1, C3, C7: 100nF; C_0805_2012Metric
C2: 220uF; CP_Elec_6.3x7.7; LCSC C280399
C4: 100uF; CP_EIA-3528-21_Kemet-B; LCSC C16133
C5, C6: 10uF; C_0805_2012Metric
D1, D4, D7: K24; D_SMF; LCSC C5199107
D2: SMF5V0A; D_SMF
D3: SMF12A; D_SMF
D5, D6, D8, D9, D10, D11: PESD3V3; D_SOD-523; LCSC C5180303
D12, D13: PESD5V0; D_SOD-523; LCSC C19725076
H1: MountingHole; MountingHole_2.7mm_M2.5
J1: USB C; MC-803LS-HXXX; LCSC C3039302
J2: XT30UPB; AMASS_XT30UPB-M_1x02_P5.0mm_Vertical; LCSC C428721
J3: Column Connector; Samtec_HLE-107-02-xxx-DV-BE-A_2x07_P2.54mm_Horizontal
J4: Row Connector; IDC-Header_2x09_P2.54mm_Vertical
L1: 68uH; L_Sunlord_SWPA6045S; LCSC C53663
LED1: WS2812B-2020; LED_WS2812B-2020_PLCC4_2.0x2.0mm; LCSC C41413181
R1: 10K; R_0603_1608Metric
R2, R3: 5K1; R_0603_1608Metric
R4: 220K; R_0603_1608Metric
R5: 20K; R_0603_1608Metric
SW1: BOOT; SW_SPST_EVQP7C; LCSC C528965
SW2: RESET; SW_SPST_EVQP7C; LCSC C528965
TP0, TP1, TP2, TP3, TP4, TP5, TP6, TP7, TP8, TP9, TP10, TP11: TestPoint; TestPoint_Pad_D1.5mm
U1: XL1509-5.0; SOIC-8_3.9x4.9mm_P1.27mm; LCSC C61063
U2: ESP32-S3-WROOM-1
U3: AP2112K-3.3; SOT-23-5

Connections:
+3V3: C6.1, C7.1, R1.2, TP8.1, U2.2 (3V3), U3.5 (VOUT)
+5V: C4.1, C5.1, D1.1 (K), D7.1 (K), J3.7, J3.9, LED1.4 (VDD), TP6.1, U1.3 (FB), U3.1 (VIN), U3.3 (EN)
+12V: C2.1, C3.1, D3.1 (A1), J2.2, J3.11, J3.13, J3.14, J4.11, J4.13, J4.14, J4.15, J4.16, J4.17, J4.18, R4.1, U1.1 (VIN)
/12V OK: R4.2, R5.1, U2.20 (GPIO12/TOUCH12/ADC2_CH1/FSPICLK/FSPIIO6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)
/COL START: D11.1 (K), J3.3, TP5.1, U2.38 (GPIO2/TOUCH2/ADC1_CH1)
/DLED: LED1.3 (DIN), U2.18 (GPIO10/TOUCH10/ADC1_CH9/FSPICS0/FSPIIO4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)
/EN: C1.2, R1.1, SW2.1, TP11.1, U2.3 (EN)
/IO0: SW1.1, TP4.1, U2.27 (GPIO0/BOOT)
/ROW START: D10.1 (K), J4.4, U2.6 (GPIO6/TOUCH6/ADC1_CH5)
/UART0_RX: TP1.1, U2.36 (U0RXD/GPIO44/CLK_OUT2)
/UART0_TX: TP0.1, U2.37 (U0TXD/GPIO43/CLK_OUT1)
/UART1_RX_A: D5.1 (K), J4.1, U2.4 (GPIO4/TOUCH4/ADC1_CH3)
/UART1_RX_B: D8.1 (K), J3.1, TP10.1, U2.25 (GPIO48/SPICLK_N/SUBSPICLK_N_DIFF)
/UART1_TX_A: D6.1 (K), J4.2, U2.5 (GPIO5/TOUCH5/ADC1_CH4)
/UART1_TX_B: D9.1 (K), J3.2, TP9.1, U2.24 (GPIO47/SPICLK_P/SUBSPICLK_P_DIFF)
/USB_D+: D13.1 (K), J1.A6 (D+), J1.B6 (D+), TP2.1, U2.14 (GPIO20/U1CTS/ADC2_CH9/CLK_OUT1/USB_D+)
/USB_D-: D12.1 (K), J1.A7 (D-), J1.B7 (D-), TP3.1, U2.13 (GPIO19/U1RTS/ADC2_CH8/CLK_OUT2/USB_D-)
GND: C1.1, C2.2, C3.2, C4.2, C5.2, C6.2, C7.2, D2.2 (A2), D3.2 (A2), D4.2 (A), D5.2 (A), D6.2 (A), D8.2 (A), D9.2 (A), D10.2 (A), D11.2 (A), D12.2 (A), D13.2 (A), J1.A1 (GND), J1.A12 (GND), J1.B1 (GND), J1.B12 (GND), J1.S1 (SHIELD), J2.1, J3.4, J3.5, J3.6, J3.8, J3.10, J3.12, J4.3, J4.5, J4.6, J4.7, J4.8, J4.9, J4.10, J4.12, LED1.2 (VSS), R2.2, R3.2, R5.2, SW1.2, SW2.2, U1.4 (~EN), U1.5 (GND), U1.6 (GND), U1.7 (GND), U1.8 (GND), U2.1 (GND), U2.40 (GND), U2.41 (GND), U3.2 (GND)
unnamed: D4.1 (K), L1.1, U1.2 (OUT)
unnamed: D7.2 (A), L1.2
unnamed: J1.A5 (CC1), R2.1
unnamed: J1.B5 (CC2), R3.1
VBUS: D1.2 (A), D2.1 (A1), J1.A4 (VBUS), J1.A9 (VBUS), J1.B4 (VBUS), J1.B9 (VBUS), TP7.1

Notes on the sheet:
Power DC/DC
ESD
Buttons
USB Port
12V to 5V 2A Buck convertor. 5V to 3.3V 250mA LDO.
Connectors
ESP32-S3

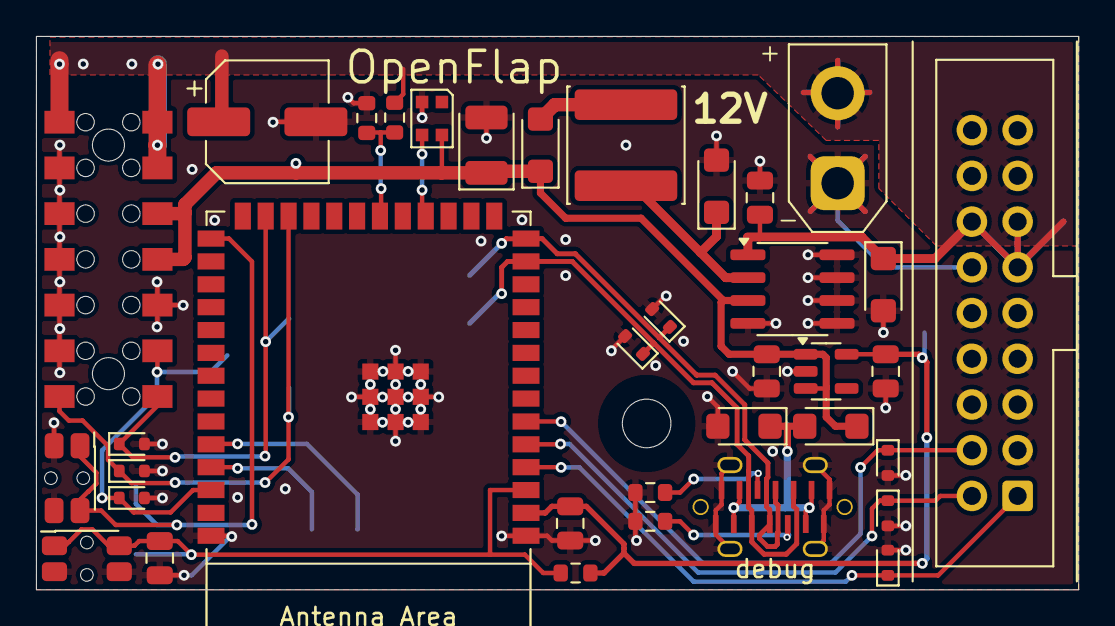
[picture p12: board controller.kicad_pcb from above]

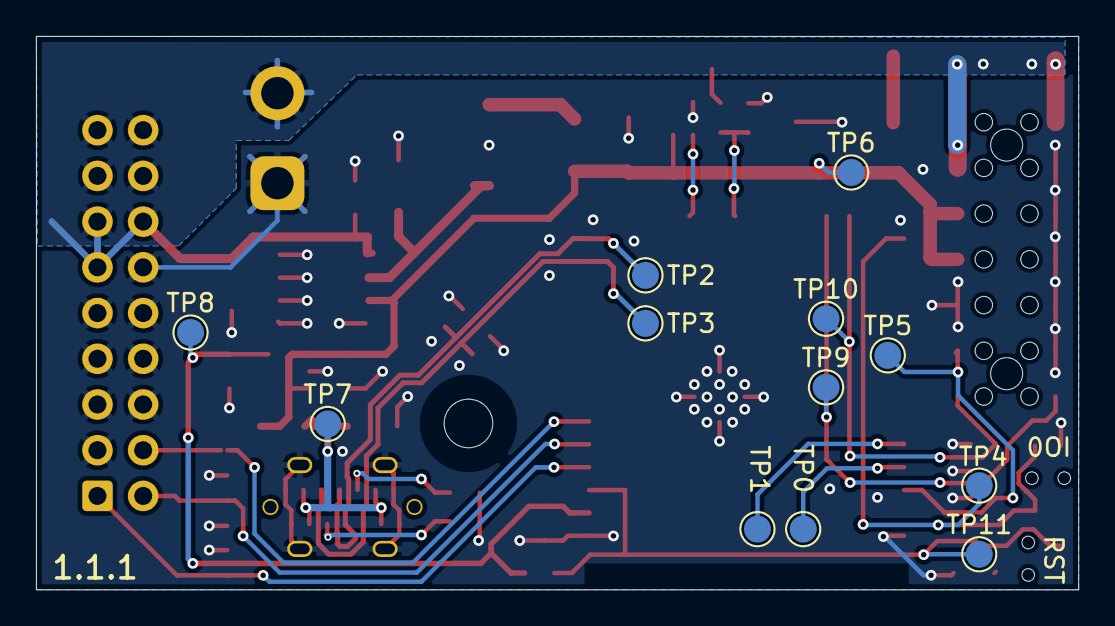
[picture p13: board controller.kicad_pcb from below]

Board: 2 copper layers, 57.9 x 30.7 mm, 49 parts (12 on the bottom side), 23 nets.

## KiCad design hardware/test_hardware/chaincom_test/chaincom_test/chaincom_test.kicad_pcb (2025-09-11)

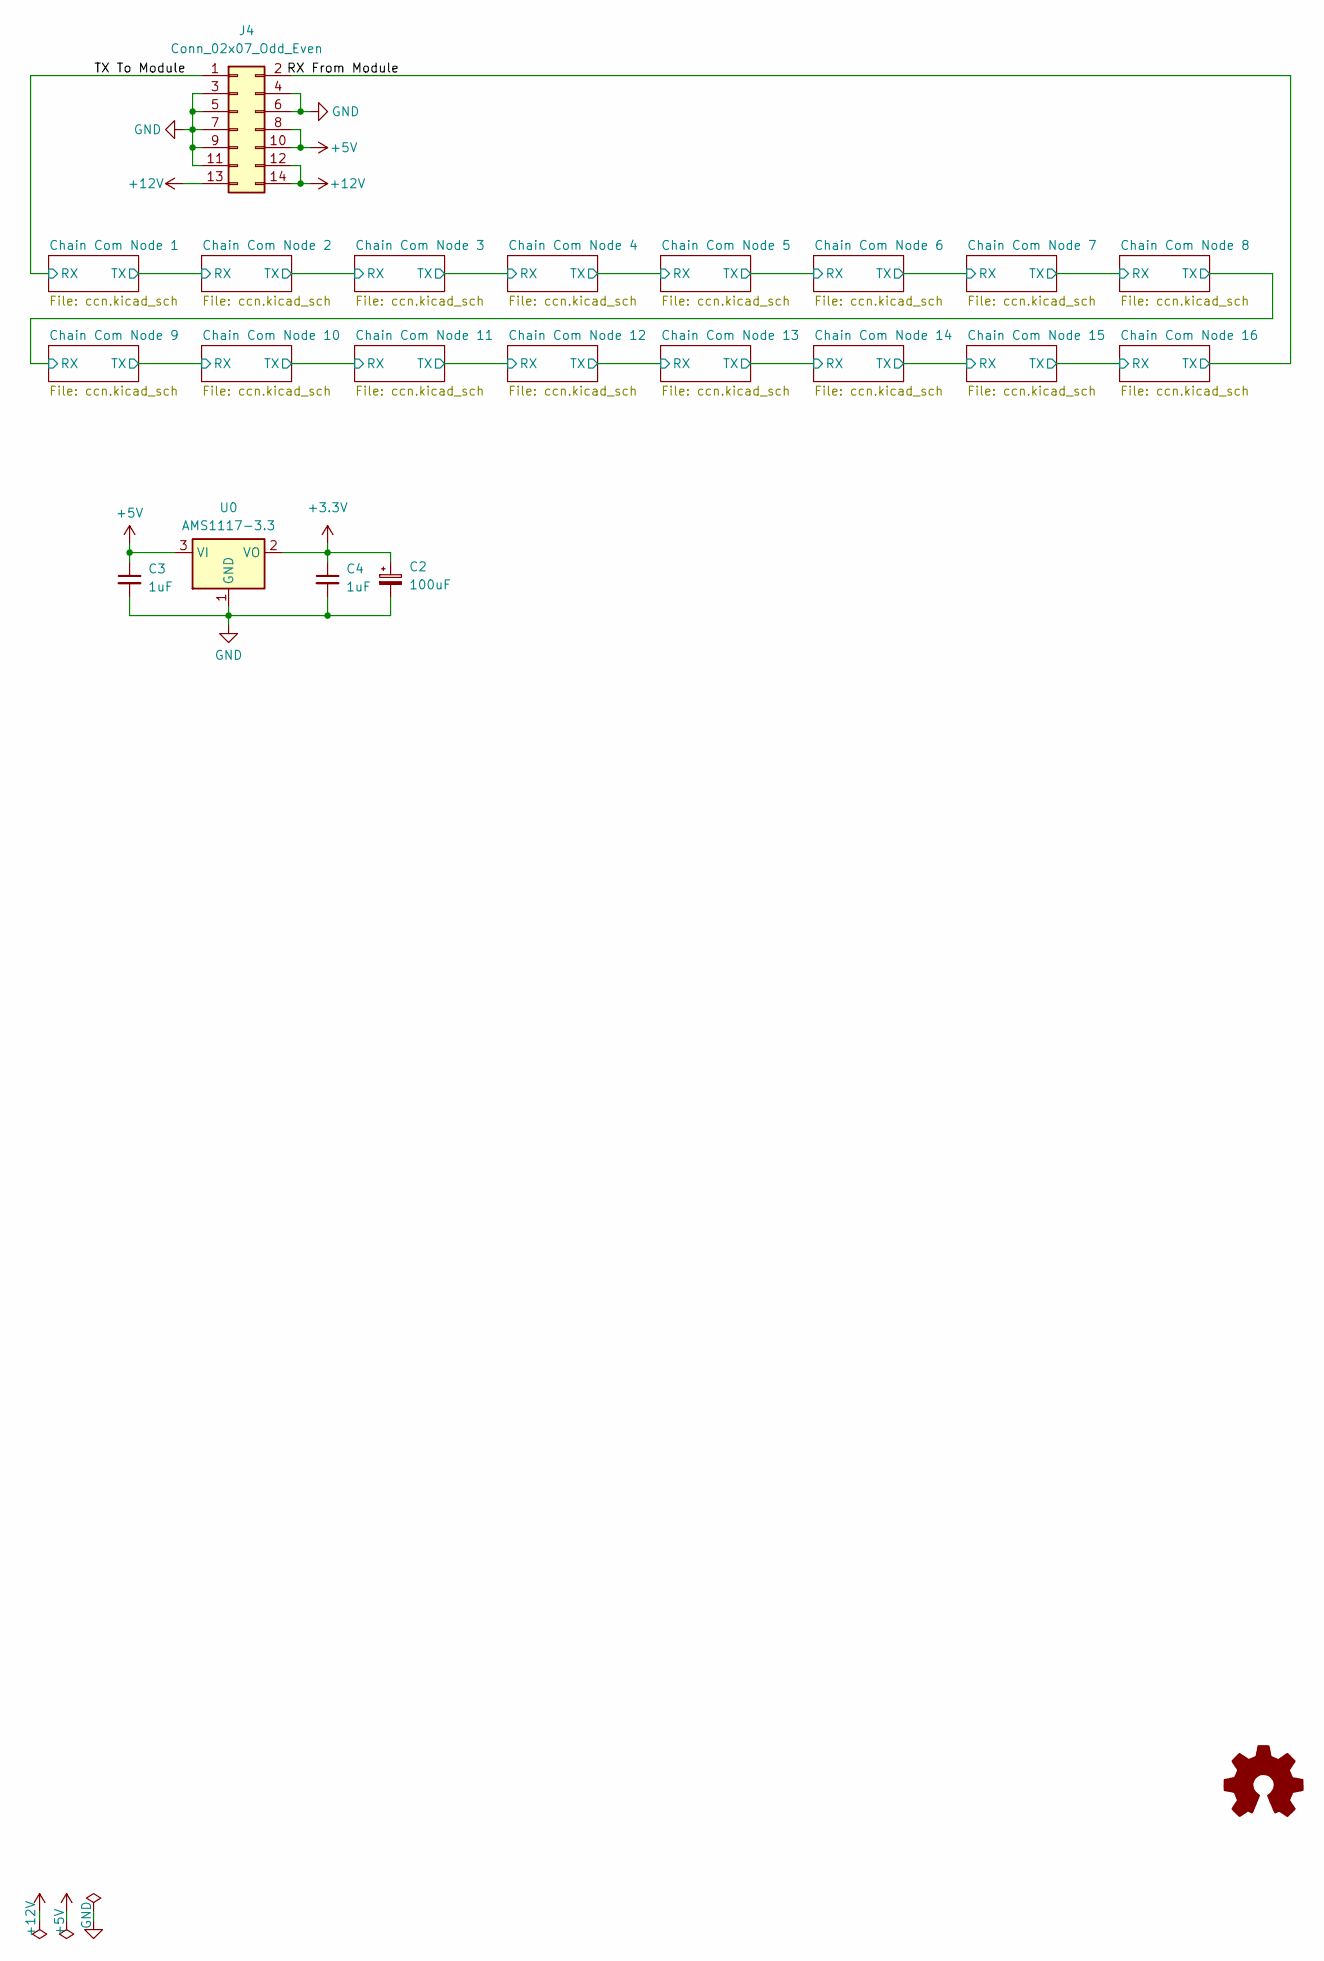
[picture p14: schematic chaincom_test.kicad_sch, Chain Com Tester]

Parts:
C2: 100uF; CP_EIA-3528-21_Kemet-B; LCSC C16133
C3, C4: 1uF; C_0805_2012Metric
J4: Conn_02x07_Odd_Even; PinHeader_2x07_P2.54mm_Vertical
U0: AMS1117-3.3; SOT-223-3_TabPin2; LCSC C18164485

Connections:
+3.3V: C2.1, C4.1, U0.2 (VO); also elsewhere on the board
+5V: C3.1, J4.8, J4.10, U0.3 (VI)
+12V: J4.12, J4.13, J4.14
/RX From Module: J4.2; also elsewhere on the board
/TX To Module: J4.1; also elsewhere on the board
GND: C2.2, C3.2, C4.2, J4.3, J4.4, J4.5, J4.6, J4.7, J4.9, J4.11, U0.1 (GND); also elsewhere on the board

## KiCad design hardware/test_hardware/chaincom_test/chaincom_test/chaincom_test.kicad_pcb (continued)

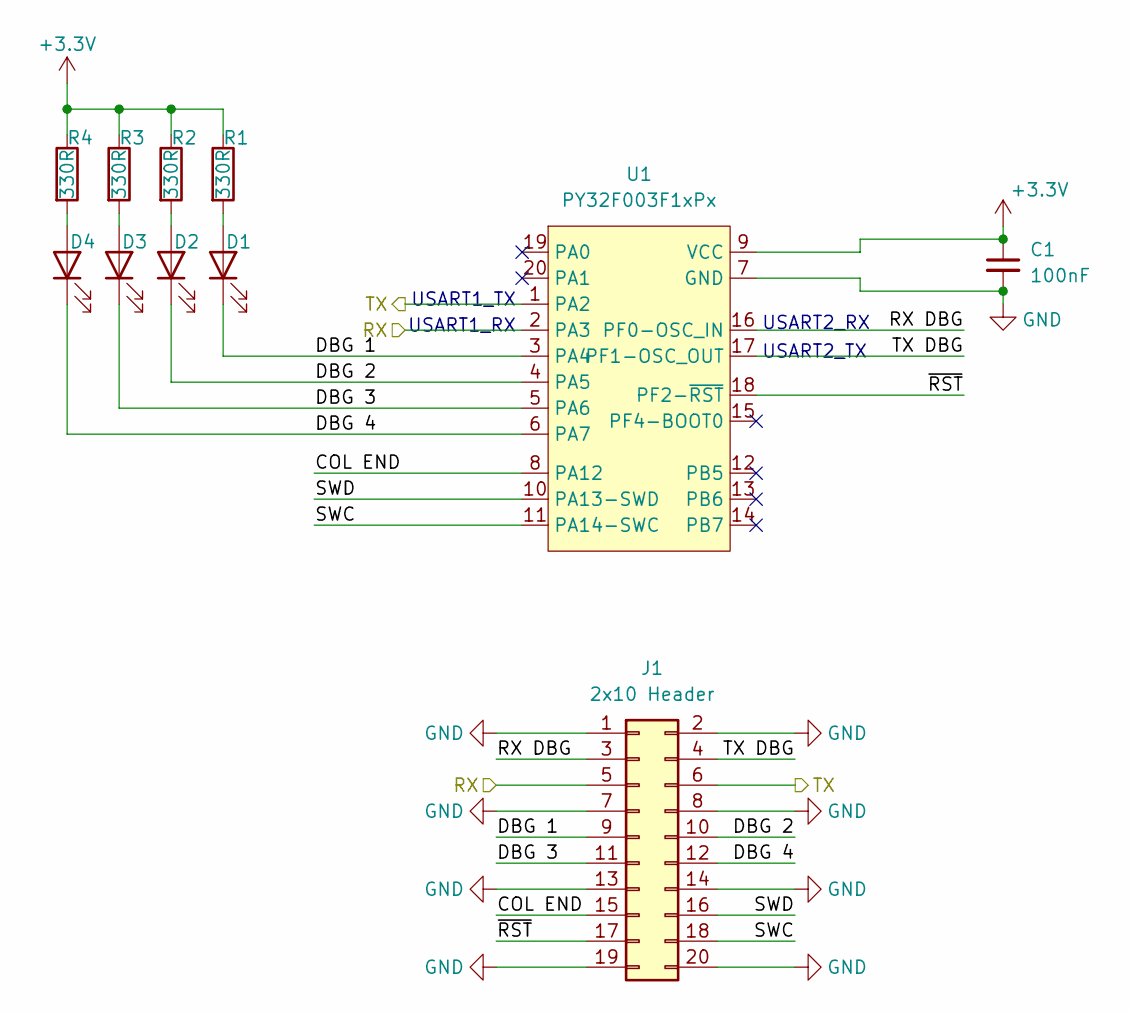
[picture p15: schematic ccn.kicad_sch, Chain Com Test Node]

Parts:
C1: 100nF; C_0805_2012Metric
D1: XL-1608UBC-06A; LED_0603_1608Metric; LCSC C7371904
D2: XL-1608SYGC-06; LED_0603_1608Metric; LCSC C965805
D3: XL-1608UOC-06; LED_0603_1608Metric; LCSC C965800
D4: XL-1608SURC-06; LED_0603_1608Metric; LCSC C965799
J1: 2x10 Header; PinHeader_2x10_P2.54mm_Vertical
R1, R2, R3, R4: 330R; R_0805_2012Metric
U1: PY32F003F1xPx; TSSOP-20_4.4x6.5mm_P0.65mm; LCSC C5379864

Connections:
+3.3V: C1.1, R1.1, R2.1, R3.1, R4.1, U1.9 (VCC); also elsewhere on the board
/Chain Com Node 1/COL END: J1.15, U1.8 (PA12)
/Chain Com Node 1/DBG 1: D1.1 (K), J1.9, U1.3 (PA4)
/Chain Com Node 1/DBG 2: D2.1 (K), J1.10, U1.4 (PA5)
/Chain Com Node 1/DBG 3: D3.1 (K), J1.11, U1.5 (PA6)
/Chain Com Node 1/DBG 4: D4.1 (K), J1.12, U1.6 (PA7)
/Chain Com Node 1/RX DBG: J1.3, U1.16 (PF0-OSC_IN)
/Chain Com Node 1/SWC: J1.18, U1.11 (PA14-SWC)
/Chain Com Node 1/SWD: J1.16, U1.10 (PA13-SWD)
/Chain Com Node 1/TX: J1.6, U1.1 (PA2); also elsewhere on the board
/Chain Com Node 1/TX DBG: J1.4, U1.17 (PF1-OSC_OUT)
/Chain Com Node 1/~RST: J1.17, U1.18 (PF2-~RST)
/TX To Module: J1.5, U1.2 (PA3); also elsewhere on the board
GND: C1.2, J1.1, J1.2, J1.7, J1.8, J1.13, J1.14, J1.19, J1.20, U1.7 (GND); also elsewhere on the board
unnamed: D1.2 (A), R1.2
unnamed: D2.2 (A), R2.2
unnamed: D3.2 (A), R3.2
unnamed: D4.2 (A), R4.2

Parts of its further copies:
C5, C6, C7, C8, C9, C10, C11, C12, C13, C14, C15, C16, C17, C18, C19: 100nF; C_0805_2012Metric
D5, D9, D13, D17, D21, D25, D29, D33, D37, D41, D45, D49, D53, D57, D61: XL-1608SURC-06; LED_0603_1608Metric; LCSC C965799
D6, D10, D14, D18, D22, D26, D30, D34, D38, D42, D46, D50, D54, D58, D62: XL-1608UOC-06; LED_0603_1608Metric; LCSC C965800
D7, D11, D15, D19, D23, D27, D31, D35, D39, D43, D47, D51, D55, D59, D63: XL-1608SYGC-06; LED_0603_1608Metric; LCSC C965805
D8, D12, D16, D20, D24, D28, D32, D36, D40, D44, D48, D52, D56, D60, D64: XL-1608UBC-06A; LED_0603_1608Metric; LCSC C7371904
J2, J3, J5, J6, J7, J8, J9, J10, J11, J12, J13, J14, J15, J16, J17: 2x10 Header; PinHeader_2x10_P2.54mm_Vertical
R5, R6, R7, R8, R9, R10, R11, R12, R13, R14, R15, R16, R17, R18, R19, R20, R21, R22, R23, R24, R25, R26, R27, R28, R29, R30, R31, R32, R33, R34, R35, R36, R37, R38, R39, R40, R41, R42, R43, R44, R45, R46, R47, R48, R49, R50, R51, R52, R53, R54, R55, R56, R57, R58, R59, R60, R61, R62, R63, R64: 330R; R_0805_2012Metric
U2, U3, U4, U5, U6, U7, U8, U9, U10, U11, U12, U13, U14, U15, U16: PY32F003F1xPx; TSSOP-20_4.4x6.5mm_P0.65mm; LCSC C5379864

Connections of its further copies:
+3.3V: C5.1, C6.1, C7.1, C8.1, C9.1, C10.1, C11.1, C12.1, C13.1, C14.1, C15.1, C16.1, C17.1, C18.1, C19.1, R5.1, R6.1, R7.1, R8.1, R9.1, R10.1, R11.1, R12.1, R13.1, R14.1, R15.1, R16.1, R17.1, R18.1, R19.1, R20.1, R21.1, R22.1, R23.1, R24.1, R25.1, R26.1, R27.1, R28.1, R29.1, R30.1, R31.1, R32.1, R33.1, R34.1, R35.1, R36.1, R37.1, R38.1, R39.1, R40.1, R41.1, R42.1, R43.1, R44.1, R45.1, R46.1, R47.1, R48.1, R49.1, R50.1, R51.1, R52.1, R53.1, R54.1, R55.1, R56.1, R57.1, R58.1, R59.1, R60.1, R61.1, R62.1, R63.1, R64.1, U2.9 (VCC), U3.9 (VCC), U4.9 (VCC), U5.9 (VCC), U6.9 (VCC), U7.9 (VCC), U8.9 (VCC), U9.9 (VCC), U10.9 (VCC), U11.9 (VCC), U12.9 (VCC), U13.9 (VCC), U14.9 (VCC), U15.9 (VCC), U16.9 (VCC); also elsewhere on the board
/Chain Com Node 1/TX: J2.5, U2.2 (PA3); also elsewhere on the board
/Chain Com Node 2/COL END: J2.15, U2.8 (PA12)
/Chain Com Node 2/DBG 1: D8.1 (K), J2.9, U2.3 (PA4)
/Chain Com Node 2/DBG 2: D7.1 (K), J2.10, U2.4 (PA5)
/Chain Com Node 2/DBG 3: D6.1 (K), J2.11, U2.5 (PA6)
/Chain Com Node 2/DBG 4: D5.1 (K), J2.12, U2.6 (PA7)
/Chain Com Node 2/RX DBG: J2.3, U2.16 (PF0-OSC_IN)
/Chain Com Node 2/SWC: J2.18, U2.11 (PA14-SWC)
/Chain Com Node 2/SWD: J2.16, U2.10 (PA13-SWD)
/Chain Com Node 2/TX: J2.6, J3.5, U2.1 (PA2), U3.2 (PA3)
/Chain Com Node 2/TX DBG: J2.4, U2.17 (PF1-OSC_OUT)
/Chain Com Node 2/~RST: J2.17, U2.18 (PF2-~RST)
/Chain Com Node 3/COL END: J3.15, U3.8 (PA12)
/Chain Com Node 3/DBG 1: D12.1 (K), J3.9, U3.3 (PA4)
/Chain Com Node 3/DBG 2: D11.1 (K), J3.10, U3.4 (PA5)
/Chain Com Node 3/DBG 3: D10.1 (K), J3.11, U3.5 (PA6)
/Chain Com Node 3/DBG 4: D9.1 (K), J3.12, U3.6 (PA7)
/Chain Com Node 3/RX DBG: J3.3, U3.16 (PF0-OSC_IN)
/Chain Com Node 3/SWC: J3.18, U3.11 (PA14-SWC)
/Chain Com Node 3/SWD: J3.16, U3.10 (PA13-SWD)
/Chain Com Node 3/TX: J3.6, J5.5, U3.1 (PA2), U4.2 (PA3)
/Chain Com Node 3/TX DBG: J3.4, U3.17 (PF1-OSC_OUT)
/Chain Com Node 3/~RST: J3.17, U3.18 (PF2-~RST)
/Chain Com Node 4/COL END: J5.15, U4.8 (PA12)
/Chain Com Node 4/DBG 1: D16.1 (K), J5.9, U4.3 (PA4)
/Chain Com Node 4/DBG 2: D15.1 (K), J5.10, U4.4 (PA5)
/Chain Com Node 4/DBG 3: D14.1 (K), J5.11, U4.5 (PA6)
/Chain Com Node 4/DBG 4: D13.1 (K), J5.12, U4.6 (PA7)
/Chain Com Node 4/RX DBG: J5.3, U4.16 (PF0-OSC_IN)
/Chain Com Node 4/SWC: J5.18, U4.11 (PA14-SWC)
/Chain Com Node 4/SWD: J5.16, U4.10 (PA13-SWD)
/Chain Com Node 4/TX: J5.6, J6.5, U4.1 (PA2), U5.2 (PA3)
/Chain Com Node 4/TX DBG: J5.4, U4.17 (PF1-OSC_OUT)
/Chain Com Node 4/~RST: J5.17, U4.18 (PF2-~RST)
/Chain Com Node 5/COL END: J6.15, U5.8 (PA12)
/Chain Com Node 5/DBG 1: D20.1 (K), J6.9, U5.3 (PA4)
/Chain Com Node 5/DBG 2: D19.1 (K), J6.10, U5.4 (PA5)
/Chain Com Node 5/DBG 3: D18.1 (K), J6.11, U5.5 (PA6)
/Chain Com Node 5/DBG 4: D17.1 (K), J6.12, U5.6 (PA7)
/Chain Com Node 5/RX DBG: J6.3, U5.16 (PF0-OSC_IN)
/Chain Com Node 5/SWC: J6.18, U5.11 (PA14-SWC)
/Chain Com Node 5/SWD: J6.16, U5.10 (PA13-SWD)
/Chain Com Node 5/TX: J6.6, J7.5, U5.1 (PA2), U6.2 (PA3)
/Chain Com Node 5/TX DBG: J6.4, U5.17 (PF1-OSC_OUT)
/Chain Com Node 5/~RST: J6.17, U5.18 (PF2-~RST)
/Chain Com Node 6/COL END: J7.15, U6.8 (PA12)
/Chain Com Node 6/DBG 1: D24.1 (K), J7.9, U6.3 (PA4)
/Chain Com Node 6/DBG 2: D23.1 (K), J7.10, U6.4 (PA5)
/Chain Com Node 6/DBG 3: D22.1 (K), J7.11, U6.5 (PA6)
/Chain Com Node 6/DBG 4: D21.1 (K), J7.12, U6.6 (PA7)
/Chain Com Node 6/RX DBG: J7.3, U6.16 (PF0-OSC_IN)
/Chain Com Node 6/SWC: J7.18, U6.11 (PA14-SWC)
/Chain Com Node 6/SWD: J7.16, U6.10 (PA13-SWD)
/Chain Com Node 6/TX: J7.6, J8.5, U6.1 (PA2), U7.2 (PA3)
/Chain Com Node 6/TX DBG: J7.4, U6.17 (PF1-OSC_OUT)
/Chain Com Node 6/~RST: J7.17, U6.18 (PF2-~RST)
/Chain Com Node 7/COL END: J8.15, U7.8 (PA12)
/Chain Com Node 7/DBG 1: D28.1 (K), J8.9, U7.3 (PA4)
/Chain Com Node 7/DBG 2: D27.1 (K), J8.10, U7.4 (PA5)
/Chain Com Node 7/DBG 3: D26.1 (K), J8.11, U7.5 (PA6)
/Chain Com Node 7/DBG 4: D25.1 (K), J8.12, U7.6 (PA7)
/Chain Com Node 7/RX DBG: J8.3, U7.16 (PF0-OSC_IN)
/Chain Com Node 7/SWC: J8.18, U7.11 (PA14-SWC)
/Chain Com Node 7/SWD: J8.16, U7.10 (PA13-SWD)
/Chain Com Node 7/TX: J8.6, J9.5, U7.1 (PA2), U8.2 (PA3)
/Chain Com Node 7/TX DBG: J8.4, U7.17 (PF1-OSC_OUT)
/Chain Com Node 7/~RST: J8.17, U7.18 (PF2-~RST)
/Chain Com Node 8/COL END: J9.15, U8.8 (PA12)
/Chain Com Node 8/DBG 1: D32.1 (K), J9.9, U8.3 (PA4)
/Chain Com Node 8/DBG 2: D31.1 (K), J9.10, U8.4 (PA5)
/Chain Com Node 8/DBG 3: D30.1 (K), J9.11, U8.5 (PA6)
/Chain Com Node 8/DBG 4: D29.1 (K), J9.12, U8.6 (PA7)
/Chain Com Node 8/RX DBG: J9.3, U8.16 (PF0-OSC_IN)
/Chain Com Node 8/SWC: J9.18, U8.11 (PA14-SWC)
/Chain Com Node 8/SWD: J9.16, U8.10 (PA13-SWD)
/Chain Com Node 8/TX: J9.6, J10.5, U8.1 (PA2), U9.2 (PA3)
/Chain Com Node 8/TX DBG: J9.4, U8.17 (PF1-OSC_OUT)
/Chain Com Node 8/~RST: J9.17, U8.18 (PF2-~RST)
/Chain Com Node 9/COL END: J10.15, U9.8 (PA12)
/Chain Com Node 9/DBG 1: D36.1 (K), J10.9, U9.3 (PA4)
/Chain Com Node 9/DBG 2: D35.1 (K), J10.10, U9.4 (PA5)
/Chain Com Node 9/DBG 3: D34.1 (K), J10.11, U9.5 (PA6)
/Chain Com Node 9/DBG 4: D33.1 (K), J10.12, U9.6 (PA7)
/Chain Com Node 9/RX DBG: J10.3, U9.16 (PF0-OSC_IN)
/Chain Com Node 9/SWC: J10.18, U9.11 (PA14-SWC)
/Chain Com Node 9/SWD: J10.16, U9.10 (PA13-SWD)
/Chain Com Node 9/TX DBG: J10.4, U9.17 (PF1-OSC_OUT)
/Chain Com Node 9/~RST: J10.17, U9.18 (PF2-~RST)
/Chain Com Node 10/COL END: J11.15, U10.8 (PA12)
/Chain Com Node 10/DBG 1: D40.1 (K), J11.9, U10.3 (PA4)
/Chain Com Node 10/DBG 2: D39.1 (K), J11.10, U10.4 (PA5)
/Chain Com Node 10/DBG 3: D38.1 (K), J11.11, U10.5 (PA6)
/Chain Com Node 10/DBG 4: D37.1 (K), J11.12, U10.6 (PA7)
/Chain Com Node 10/RX: J10.6, J11.5, U9.1 (PA2), U10.2 (PA3)
/Chain Com Node 10/RX DBG: J11.3, U10.16 (PF0-OSC_IN)
/Chain Com Node 10/SWC: J11.18, U10.11 (PA14-SWC)
/Chain Com Node 10/SWD: J11.16, U10.10 (PA13-SWD)
/Chain Com Node 10/TX: J11.6, J12.5, U10.1 (PA2), U11.2 (PA3)
/Chain Com Node 10/TX DBG: J11.4, U10.17 (PF1-OSC_OUT)
/Chain Com Node 10/~RST: J11.17, U10.18 (PF2-~RST)
/Chain Com Node 11/COL END: J12.15, U11.8 (PA12)
/Chain Com Node 11/DBG 1: D44.1 (K), J12.9, U11.3 (PA4)
/Chain Com Node 11/DBG 2: D43.1 (K), J12.10, U11.4 (PA5)
/Chain Com Node 11/DBG 3: D42.1 (K), J12.11, U11.5 (PA6)
/Chain Com Node 11/DBG 4: D41.1 (K), J12.12, U11.6 (PA7)
/Chain Com Node 11/RX DBG: J12.3, U11.16 (PF0-OSC_IN)
/Chain Com Node 11/SWC: J12.18, U11.11 (PA14-SWC)
/Chain Com Node 11/SWD: J12.16, U11.10 (PA13-SWD)
/Chain Com Node 11/TX: J12.6, J13.5, U11.1 (PA2), U12.2 (PA3)
/Chain Com Node 11/TX DBG: J12.4, U11.17 (PF1-OSC_OUT)
/Chain Com Node 11/~RST: J12.17, U11.18 (PF2-~RST)
/Chain Com Node 12/COL END: J13.15, U12.8 (PA12)
/Chain Com Node 12/DBG 1: D48.1 (K), J13.9, U12.3 (PA4)
/Chain Com Node 12/DBG 2: D47.1 (K), J13.10, U12.4 (PA5)
/Chain Com Node 12/DBG 3: D46.1 (K), J13.11, U12.5 (PA6)
/Chain Com Node 12/DBG 4: D45.1 (K), J13.12, U12.6 (PA7)
/Chain Com Node 12/RX DBG: J13.3, U12.16 (PF0-OSC_IN)
/Chain Com Node 12/SWC: J13.18, U12.11 (PA14-SWC)
/Chain Com Node 12/SWD: J13.16, U12.10 (PA13-SWD)
/Chain Com Node 12/TX: J13.6, J14.5, U12.1 (PA2), U13.2 (PA3)
/Chain Com Node 12/TX DBG: J13.4, U12.17 (PF1-OSC_OUT)
/Chain Com Node 12/~RST: J13.17, U12.18 (PF2-~RST)
/Chain Com Node 13/COL END: J14.15, U13.8 (PA12)
/Chain Com Node 13/DBG 1: D52.1 (K), J14.9, U13.3 (PA4)
/Chain Com Node 13/DBG 2: D51.1 (K), J14.10, U13.4 (PA5)
/Chain Com Node 13/DBG 3: D50.1 (K), J14.11, U13.5 (PA6)
/Chain Com Node 13/DBG 4: D49.1 (K), J14.12, U13.6 (PA7)
/Chain Com Node 13/RX DBG: J14.3, U13.16 (PF0-OSC_IN)
/Chain Com Node 13/SWC: J14.18, U13.11 (PA14-SWC)
/Chain Com Node 13/SWD: J14.16, U13.10 (PA13-SWD)
/Chain Com Node 13/TX: J14.6, J15.5, U13.1 (PA2), U14.2 (PA3)
/Chain Com Node 13/TX DBG: J14.4, U13.17 (PF1-OSC_OUT)
/Chain Com Node 13/~RST: J14.17, U13.18 (PF2-~RST)
/Chain Com Node 14/COL END: J15.15, U14.8 (PA12)
/Chain Com Node 14/DBG 1: D56.1 (K), J15.9, U14.3 (PA4)
/Chain Com Node 14/DBG 2: D55.1 (K), J15.10, U14.4 (PA5)
/Chain Com Node 14/DBG 3: D54.1 (K), J15.11, U14.5 (PA6)
/Chain Com Node 14/DBG 4: D53.1 (K), J15.12, U14.6 (PA7)
/Chain Com Node 14/RX DBG: J15.3, U14.16 (PF0-OSC_IN)
/Chain Com Node 14/SWC: J15.18, U14.11 (PA14-SWC)
/Chain Com Node 14/SWD: J15.16, U14.10 (PA13-SWD)
/Chain Com Node 14/TX: J15.6, J16.5, U14.1 (PA2), U15.2 (PA3)
/Chain Com Node 14/TX DBG: J15.4, U14.17 (PF1-OSC_OUT)
/Chain Com Node 14/~RST: J15.17, U14.18 (PF2-~RST)
/Chain Com Node 15/COL END: J16.15, U15.8 (PA12)
/Chain Com Node 15/DBG 1: D60.1 (K), J16.9, U15.3 (PA4)
/Chain Com Node 15/DBG 2: D59.1 (K), J16.10, U15.4 (PA5)
/Chain Com Node 15/DBG 3: D58.1 (K), J16.11, U15.5 (PA6)
/Chain Com Node 15/DBG 4: D57.1 (K), J16.12, U15.6 (PA7)
/Chain Com Node 15/RX DBG: J16.3, U15.16 (PF0-OSC_IN)
/Chain Com Node 15/SWC: J16.18, U15.11 (PA14-SWC)
/Chain Com Node 15/SWD: J16.16, U15.10 (PA13-SWD)
/Chain Com Node 15/TX: J16.6, J17.5, U15.1 (PA2), U16.2 (PA3)
/Chain Com Node 15/TX DBG: J16.4, U15.17 (PF1-OSC_OUT)
/Chain Com Node 15/~RST: J16.17, U15.18 (PF2-~RST)
/Chain Com Node 16/COL END: J17.15, U16.8 (PA12)
/Chain Com Node 16/DBG 1: D64.1 (K), J17.9, U16.3 (PA4)
/Chain Com Node 16/DBG 2: D63.1 (K), J17.10, U16.4 (PA5)
/Chain Com Node 16/DBG 3: D62.1 (K), J17.11, U16.5 (PA6)
/Chain Com Node 16/DBG 4: D61.1 (K), J17.12, U16.6 (PA7)
/Chain Com Node 16/RX DBG: J17.3, U16.16 (PF0-OSC_IN)
/Chain Com Node 16/SWC: J17.18, U16.11 (PA14-SWC)
/Chain Com Node 16/SWD: J17.16, U16.10 (PA13-SWD)
/Chain Com Node 16/TX DBG: J17.4, U16.17 (PF1-OSC_OUT)
/Chain Com Node 16/~RST: J17.17, U16.18 (PF2-~RST)
/RX From Module: J17.6, U16.1 (PA2); also elsewhere on the board
GND: C5.2, C6.2, C7.2, C8.2, C9.2, C10.2, C11.2, C12.2, C13.2, C14.2, C15.2, C16.2, C17.2, C18.2, C19.2, J2.1, J2.2, J2.7, J2.8, J2.13, J2.14, J2.19, J2.20, J3.1, J3.2, J3.7, J3.8, J3.13, J3.14, J3.19, J3.20, J5.1, J5.2, J5.7, J5.8, J5.13, J5.14, J5.19, J5.20, J6.1, J6.2, J6.7, J6.8, J6.13, J6.14, J6.19, J6.20, J7.1, J7.2, J7.7, J7.8, J7.13, J7.14, J7.19, J7.20, J8.1, J8.2, J8.7, J8.8, J8.13, J8.14, J8.19, J8.20, J9.1, J9.2, J9.7, J9.8, J9.13, J9.14, J9.19, J9.20, J10.1, J10.2, J10.7, J10.8, J10.13, J10.14, J10.19, J10.20, J11.1, J11.2, J11.7, J11.8, J11.13, J11.14, J11.19, J11.20, J12.1, J12.2, J12.7, J12.8, J12.13, J12.14, J12.19, J12.20, J13.1, J13.2, J13.7, J13.8, J13.13, J13.14, J13.19, J13.20, J14.1, J14.2, J14.7, J14.8, J14.13, J14.14, J14.19, J14.20, J15.1, J15.2, J15.7, J15.8, J15.13, J15.14, J15.19, J15.20, J16.1, J16.2, J16.7, J16.8, J16.13, J16.14, J16.19, J16.20, J17.1, J17.2, J17.7, J17.8, J17.13, J17.14, J17.19, J17.20, U2.7 (GND), U3.7 (GND), U4.7 (GND), U5.7 (GND), U6.7 (GND), U7.7 (GND), U8.7 (GND), U9.7 (GND), U10.7 (GND), U11.7 (GND), U12.7 (GND), U13.7 (GND), U14.7 (GND), U15.7 (GND), U16.7 (GND); also elsewhere on the board
unnamed: D5.2 (A), R5.2
unnamed: D6.2 (A), R6.2
unnamed: D7.2 (A), R7.2
unnamed: D8.2 (A), R8.2
unnamed: D9.2 (A), R9.2
unnamed: D10.2 (A), R10.2
unnamed: D11.2 (A), R11.2
unnamed: D12.2 (A), R12.2
unnamed: D13.2 (A), R13.2
unnamed: D14.2 (A), R14.2
unnamed: D15.2 (A), R15.2
unnamed: D16.2 (A), R16.2
unnamed: D17.2 (A), R17.2
unnamed: D18.2 (A), R18.2
unnamed: D19.2 (A), R19.2
unnamed: D20.2 (A), R20.2
unnamed: D21.2 (A), R21.2
unnamed: D22.2 (A), R22.2
unnamed: D23.2 (A), R23.2
unnamed: D24.2 (A), R24.2
unnamed: D25.2 (A), R25.2
unnamed: D26.2 (A), R26.2
unnamed: D27.2 (A), R27.2
unnamed: D28.2 (A), R28.2
unnamed: D29.2 (A), R29.2
unnamed: D30.2 (A), R30.2
unnamed: D31.2 (A), R31.2
unnamed: D32.2 (A), R32.2
unnamed: D33.2 (A), R33.2
unnamed: D34.2 (A), R34.2
unnamed: D35.2 (A), R35.2
unnamed: D36.2 (A), R36.2
unnamed: D37.2 (A), R37.2
unnamed: D38.2 (A), R38.2
unnamed: D39.2 (A), R39.2
unnamed: D40.2 (A), R40.2
unnamed: D41.2 (A), R41.2
unnamed: D42.2 (A), R42.2
unnamed: D43.2 (A), R43.2
unnamed: D44.2 (A), R44.2
unnamed: D45.2 (A), R45.2
unnamed: D46.2 (A), R46.2
unnamed: D47.2 (A), R47.2
unnamed: D48.2 (A), R48.2
unnamed: D49.2 (A), R49.2
unnamed: D50.2 (A), R50.2
unnamed: D51.2 (A), R51.2
unnamed: D52.2 (A), R52.2
unnamed: D53.2 (A), R53.2
unnamed: D54.2 (A), R54.2
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

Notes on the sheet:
USART2_RX
USART2_TX
USART1_RX
USART1_TX

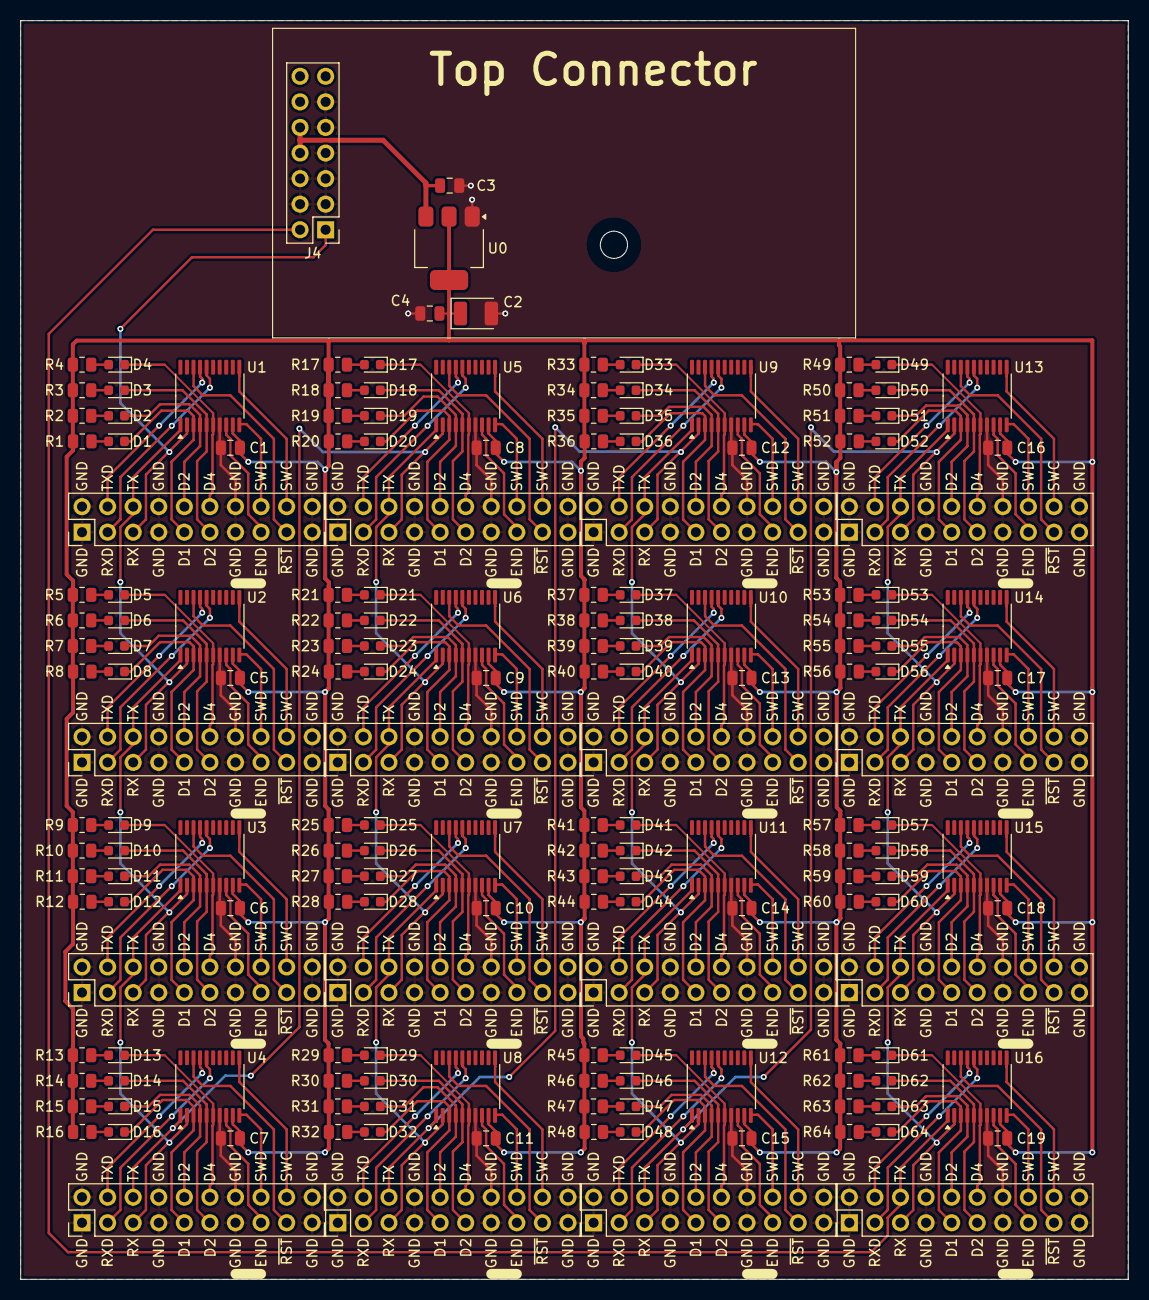
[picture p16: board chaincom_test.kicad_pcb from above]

Board: 2 copper layers, 110.0 x 125.0 mm, 182 parts (0 on the bottom side), 245 nets.

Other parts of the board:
H1: (no value)

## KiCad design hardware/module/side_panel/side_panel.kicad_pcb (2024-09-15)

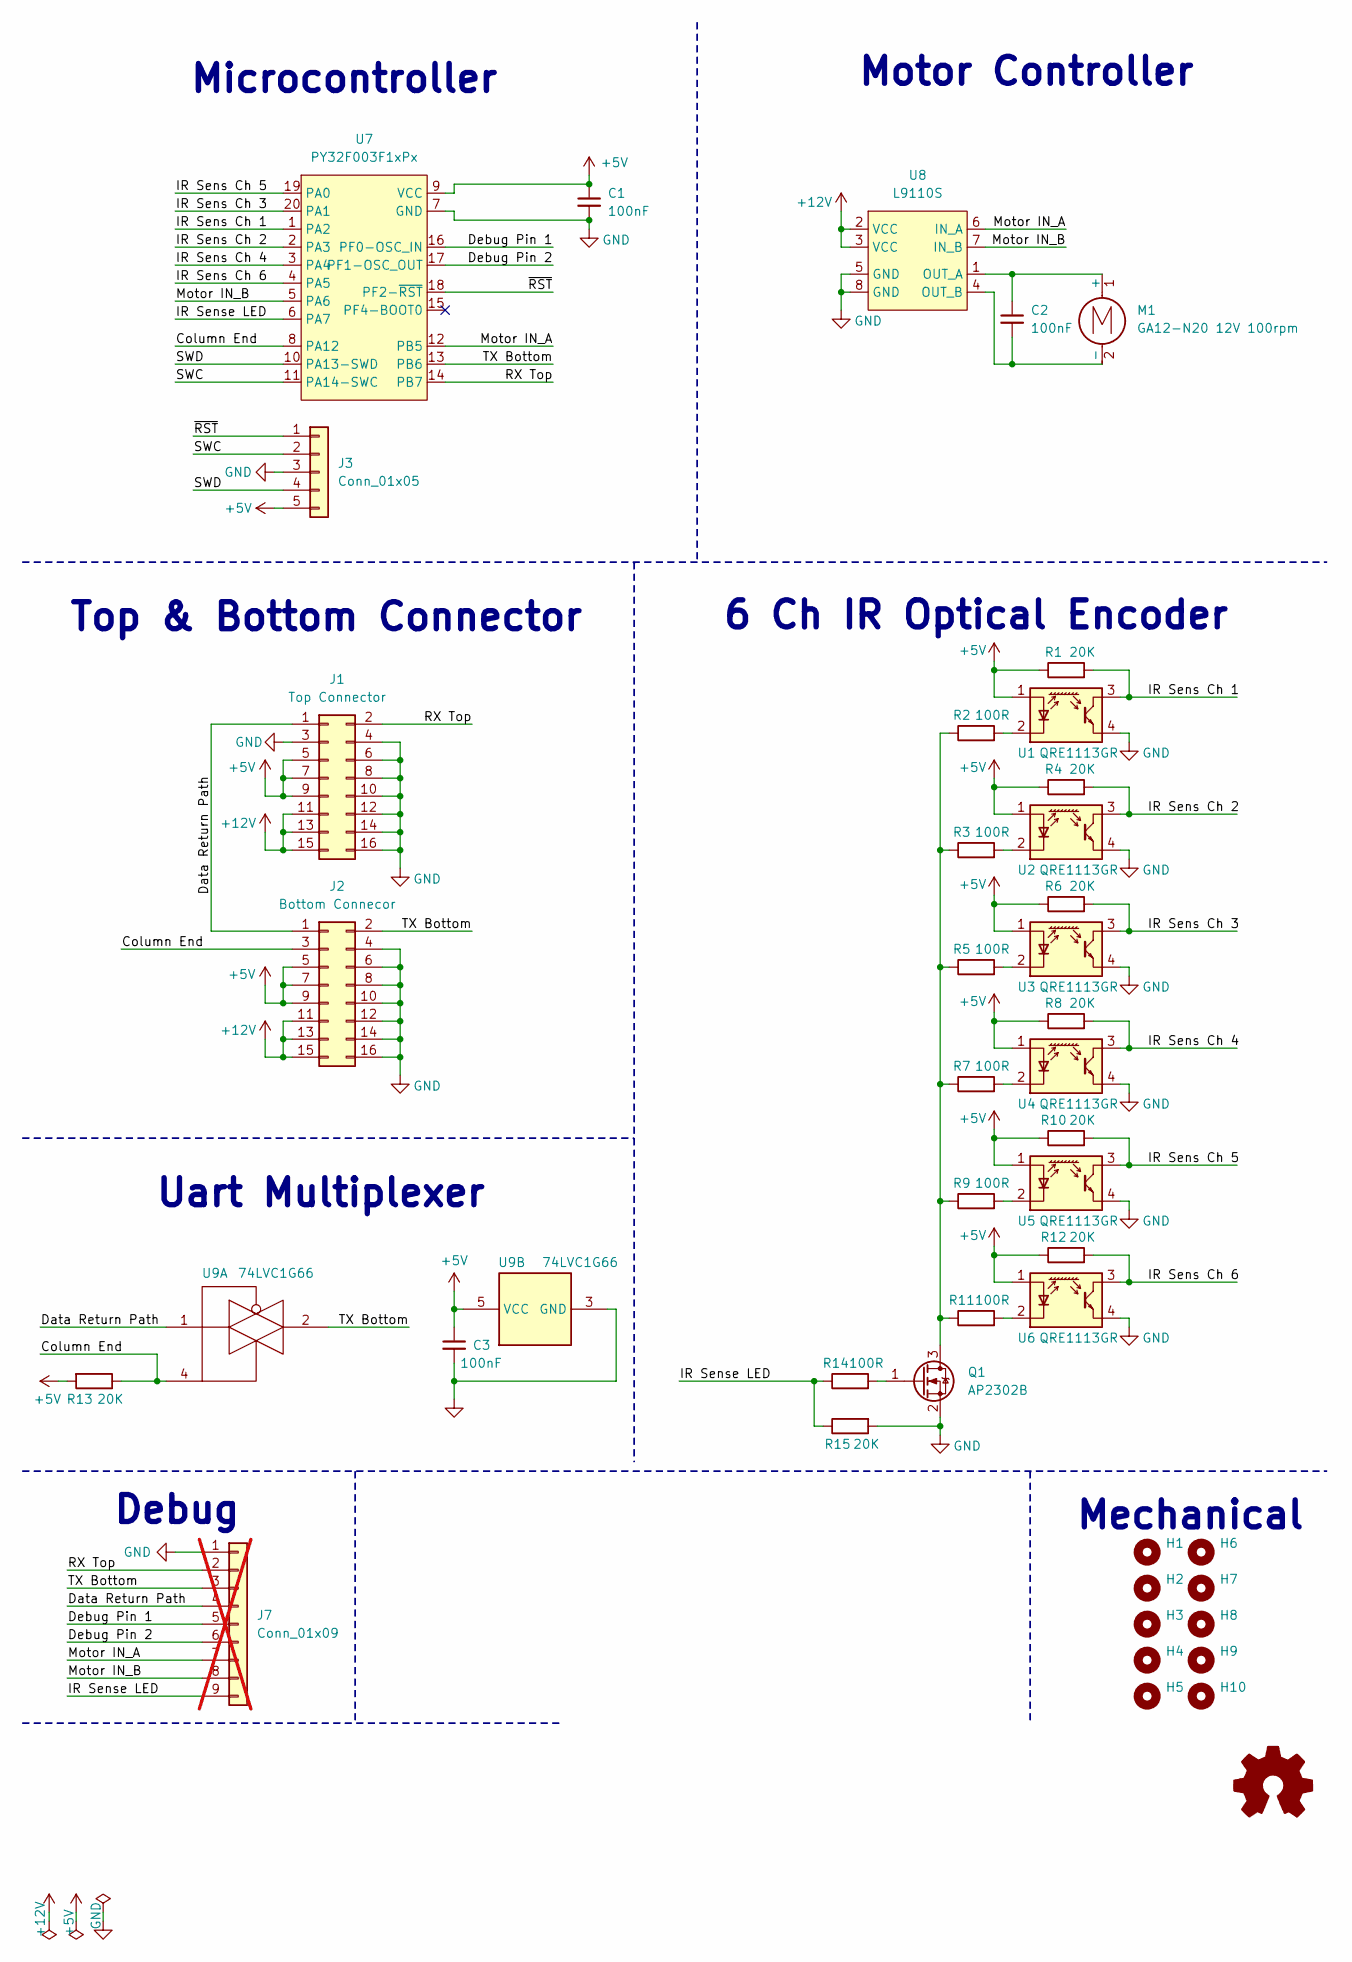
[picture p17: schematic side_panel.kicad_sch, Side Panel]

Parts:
C1, C2, C3: 100nF; C_0805_2012Metric
H1, H2, H3, H4, H5, H6, H7, H8, H9, H10: MountingHole; MountingHole_2.7mm_M2.5_ISO14580
J1: Top Connector; PinHeader_2x08_P2.54mm_Horizontal; LCSC C358710
J2: Bottom Connecor; PinSocket_2x08_P2.54mm_Horizontal; LCSC C239359
J3: Conn_01x05; PinHeader_1x05_P2.54mm_Vertical
J7: Conn_01x09; PinHeader_1x09_P2.54mm_Vertical; not fitted
M1: GA12-N20 12V 100rpm; GA12-N20 Motor Vertical
Q1: AP2302B; SOT-23; LCSC C406812
R1, R4, R6, R8, R10, R12, R13, R15: 20K; R_0805_2012Metric
R2, R3, R5, R7, R9, R11, R14: 100R; R_0805_2012Metric
U1, U2, U3, U4, U5, U6: QRE1113GR; OnSemi_CASE100CY; LCSC C81632
U7: PY32F003F1xPx; TSSOP-20_4.4x6.5mm_P0.65mm; LCSC C5379864
U8: L9110S; SOP-8_3.76x4.96mm_P1.27mm; LCSC C2984833
U9: 74LVC1G66; SOT-23-5; LCSC C5375974

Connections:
+5V: C1.1, C3.1, J1.5, J1.7, J1.9, J2.5, J2.7, J2.9, J3.5, R1.1, R4.1, R6.1, R8.1, R10.1, R12.1, R13.2, U1.1 (A), U2.1 (A), U3.1 (A), U4.1 (A), U5.1 (A), U6.1 (A), U7.9 (VCC), U9.5 (VCC)
+12V: J1.11, J1.13, J1.15, J2.11, J2.13, J2.15, U8.2 (VCC), U8.3 (VCC)
/Column End: J2.3, R13.1, U7.8 (PA12), U9.4
/Data Return Path: J1.1, J2.1, J7.4, U9.1
/Debug Pin 1: J7.5, U7.16 (PF0-OSC_IN)
/Debug Pin 2: J7.6, U7.17 (PF1-OSC_OUT)
/IR Sens Ch 1: R1.2, U1.3, U7.1 (PA2)
/IR Sens Ch 2: R4.2, U2.3, U7.2 (PA3)
/IR Sens Ch 3: R6.2, U3.3, U7.20 (PA1)
/IR Sens Ch 4: R8.2, U4.3, U7.3 (PA4)
/IR Sens Ch 5: R10.2, U5.3, U7.19 (PA0)
/IR Sens Ch 6: R12.2, U6.3, U7.4 (PA5)
/IR Sense LED: J7.9, R14.1, R15.1, U7.6 (PA7)
/Motor IN_A: J7.7, U7.12 (PB5), U8.6 (IN_A)
/Motor IN_B: J7.8, U7.5 (PA6), U8.7 (IN_B)
/RX Top: J1.2, J7.2, U7.14 (PB7)
/SWC: J3.2, U7.11 (PA14-SWC)
/SWD: J3.4, U7.10 (PA13-SWD)
/TX Bottom: J2.2, J7.3, U7.13 (PB6), U9.2
/~RST: J3.1, U7.18 (PF2-~RST)
GND: C1.2, C3.2, J1.3, J1.4, J1.6, J1.8, J1.10, J1.12, J1.14, J1.16, J2.4, J2.6, J2.8, J2.10, J2.12, J2.14, J2.16, J3.3, J7.1, Q1.2 (S), R15.2, U1.4, U2.4, U3.4, U4.4, U5.4, U6.4, U7.7 (GND), U8.5 (GND), U8.8 (GND), U9.3 (GND)
unnamed: C2.1, M1.1 (+), U8.1 (OUT_A)
unnamed: C2.2, M1.2 (-), U8.4 (OUT_B)
unnamed: Q1.3 (D), R2.1, R3.1, R5.1, R7.1, R9.1, R11.1
unnamed: Q1.1 (G), R14.2
unnamed: R2.2, U1.2 (K)
unnamed: R3.2, U2.2 (K)
unnamed: R5.2, U3.2 (K)
unnamed: R7.2, U4.2 (K)
unnamed: R9.2, U5.2 (K)
unnamed: R11.2, U6.2 (K)

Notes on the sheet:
Top & Bottom Connector
6 Ch IR Optical Encoder
Uart Multiplexer
Motor Controller
Mechanical
Microcontroller
Debug



Board: 2 copper layers, 96.0 x 120.2 mm, 45 parts (2 on the bottom side), 31 nets.

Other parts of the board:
OSHW-LOGO-1, OSHW-LOGO-2: OSHW-Logo_7.5x8mm_SilkScreen

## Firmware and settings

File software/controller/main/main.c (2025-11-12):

/**
 * \file main.c
 * \brief Main file for the controller project
 * \author Toon Van Eyck
 */

#include "controller_ota.h"
#include "driver/gpio.h"
#include "esp_app_desc.h"
#include "esp_check.h"
#include "esp_log.h"
#include "freertos/FreeRTOS.h"
#include "module_api.h"
#include "networking.h"
#include "openflap_display.h"
#include "openflap_module.h"
// #include "openflap_mdl_master.h"
#include "openflap_property_handlers.h"
#include "utils.h"
#include "webserver.h"

#include <regex.h>
#include <stdio.h>
#include <string.h>

#define TAG "MAIN"

#define STARTUP_ERROR_CHECK

void app_main(void)

{
    esp_err_t ret                 = ESP_OK; /* Set by ESP_GOTO_ON_ERROR macro. */
    const esp_app_desc_t app_desc = *esp_app_get_description();
    ESP_LOGI(TAG, "Starting OpenFlap controller: %s", app_desc.version);

    /* Connect to a network. */
    networking_config_t network_config = NETWORKING_DEFAULT_CONFIG;
    ESP_GOTO_ON_ERROR(networking_setup(&network_config), verify_firmware, TAG, "Failed to setup networking");
    networking_wait_for_connection(10000);
    ESP_LOGI(TAG, "Connected to network!");

    of_property_handlers_init();

    /* Initialize the OpenFlap display. */
    of_display_t display;
    ESP_GOTO_ON_ERROR(of_display_init(&display), verify_firmware, TAG, "Failed to initialize OpenFlap display");
    ESP_LOGI(TAG, "Display initialized!");

    /* Start the web server. */
    webserver_ctx_t webserver_ctx;
    ESP_GOTO_ON_ERROR(webserver_init(&webserver_ctx), verify_firmware, TAG, "Failed to start web server");
    ESP_LOGI(TAG, "Webserver started!");

    /* Initialize http module api. */
    ESP_GOTO_ON_ERROR(module_api_init(&webserver_ctx, &display), verify_firmware, TAG,
                      "Failed to initialize module api");
    ESP_LOGI(TAG, "Module api endpoint started!");

    /* Initialize controller OTA. */
    controller_ota_ctx_t controller_ota_ctx;
    ESP_GOTO_ON_ERROR(controller_ota_init(&controller_ota_ctx, &webserver_ctx), verify_firmware, TAG,
                      "Failed to initialize controller OTA");
    ESP_LOGI(TAG, "Controller OTA endpoint started!");

    // esp_log_level_set("*", ESP_LOG_WARN);

verify_firmware:
    /* Verify the firmware. */
    bool startup_success = (ret == ESP_OK);
    ESP_ERROR_CHECK(controller_ota_verify_firmware(startup_success));

    while (1) {
        vTaskDelay(portMAX_DELAY);
    }
}

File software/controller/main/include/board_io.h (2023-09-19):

#ifndef BOARD_IO_H
#define BOARD_IO_H

#include "driver/gpio.h"
#include "driver/ledc.h"

#define FLAP_ENABLE_PIN GPIO_NUM_2
#define MODE_BTN_PIN GPIO_NUM_33

#define LEDC_HS_TIMER LEDC_TIMER_0
#define LEDC_HS_MODE LEDC_LOW_SPEED_MODE
#define LEDC_RED_GPIO GPIO_NUM_32
#define LEDC_RED_CHANNEL LEDC_CHANNEL_0
#define LEDC_GREEN_GPIO GPIO_NUM_12
#define LEDC_GREEN_CHANNEL LEDC_CHANNEL_1
#define LEDC_BLUE_GPIO GPIO_NUM_14
#define LEDC_BLUE_CHANNEL LEDC_CHANNEL_2
#define LEDC_RGB_CH_NUM (3)
#define LEDC_RGB_DUTY (4000)
#define LEDC_RGB_FADE_TIME (3000)

void board_io_init();

void setLed(uint8_t red, uint8_t green, uint8_t blue);

#endif

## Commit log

2022-04-14 Merged 2 repositories into this fresh project repository, aptly named OpenFlap.
    [mdb_dump.txt, partition_table.csv]
2022-04-18 added enable on boot for controller and fixed issue in char_set logic
    [main.c]
2022-04-19 Fixed connection issue that broke cURL update command. Fixed bug causing the firmware update command to corrupt itself by sending a "goto_app" command. Improved the TX_DONE logic. Changed idle PWM fr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
    [flap_uart.c]
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2022-04-21 Fixed a memory allocation issue that caused consecutive web socket transmissions to be come corrupted.
2022-04-24 Added options to set wifi station and access point credentials through web UI. Added a controller reset command to the web UI.
    [main.c]
2022-04-24 Added a buffer to encoder readings to prevent false readings.
2022-04-24 Increased time between uart messages from modules to increase stability.
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2022-04-25 added 3d printing mesh files for modules
    [module_core.3mf, module_large_bearing.3mf, module_shell.3mf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]
2022-04-25 changed 3mf files to stl files for better support on github.
    [module_core.3mf, module_core.stl, module_large_bearing.3mf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]
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2022-04-27 replaced wiring diagram with by png
2022-04-27 Added linkes to 3d designs and pcb designs
    [module_shell.stl]
2022-05-03 fixed bug causing corruped encoder offsets in modules
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2022-05-12 Added production files for controller, top-con and flap. For real... Also added hardware license.
    [OpenFlap_Controller_BOM.csv, OpenFlap_Controller_CSV.csv, OpenFlap_Top-Con_BOM.csv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]
2022-05-13 Added module production files
    [OpenFlap_Module_BOM.csv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]
2022-05-24 major cleanup/rework of module firmware. The firmware now executes at fixed tick rate of 10kHz
    [main.c]
2022-05-24 fixed issues in the socket based log output causing a memory leak.
2023-06-27 Major rework of the controller and module communication. Rework of webpage. Reworked module properties.
    [module_shell.stl]
2023-07-15 Added a devcontainer supporting ESP-IDF 5.1. Fixed a bug in the offset and vtrim module view.
    [mdb_dump.txt, partition_table.csv]
2023-07-15 Add back removed files
    [mdb_dump.txt, partition_table.csv]
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2023-07-22 added eagle schematics and boards
    [encoder_wheel.brd, flap_controller.brd, flap_controller.sch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]
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2023-07-27 Updated bearing .stl files
    [module_large_bearing.stl, module_small_bearing.stl]
2023-08-02 Redrawn the 3d printed parts.
    [flap_core_for_bearings.stl, flap_hub_long.stl, flap_hub_short.stl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]
2023-08-02 Updated top-con board to use only one screw and improved the screw location
    [module_core_for_bearings.stl, module_hub_long.stl, module_hub_short.stl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]
2023-08-09 Improved the tool for assembling the flap wheels
    [flap_setter_tool.stl]
2023-09-19 Added BaseSpeed property. Reworked the way the pic stores non-volatile config. Added clang formatting Added some experimentation with mode button on controller.
    [module_core.stl, module_core_for_bearings.stl, module_shell.stl]
2023-09-20 Fixed bug in json respons from controller
    [Model.c, main.c]
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2024-03-30 fixed some property handlers and got first rotation
    [main.c]
2024-04-04 fixed chaincomm and flash storage
    [main.c]
2024-04-05 fixed flap rotation on startup
    [main.c]
2024-04-30 fix broken interrupts in app because of bootloader
2024-05-07 removed PIC firmware, module will use an ARM
    [mdb_dump.txt]
2024-06-08 Fix active/idle logic to turn active when there is communication on the uart.
    [main.c]
2024-06-19 Fixed issues with the communication protocol and added random IR sensor offset and random seed generation.
    [main.c]
2024-06-22 reworked CMAKE shared lib and fixed bug in chain_comm, disabled firmware write property
2024-07-21 major rework of the communication and uart driver
    [main.c]
2024-07-23 disable RTT debugging while communications a re ongoing as they might prevent the uart interrupt
    [Model.c, flap_uart.c, main.c]
2024-07-27 Switching to KiCad: Added top connector schematic and board
    [HLE-108-02-L-DV-BE-TR.stp, top_connector.kicad_pcb, top_connector.kicad_sch]
2024-08-03 Switching to KiCad: Added side panel schematic and board
    [GA12-N20.stp, HLE-108-02-L-DV-BE-TR.stp, side_panel.kicad_pcb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]
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2024-09-15 update kibot container to 1.7.0
    [side_panel.kicad_pcb]
2024-09-15 fix erc & drc for sidepanel
    [side_panel.kicad_pcb]
2024-09-16 Use kibot on sidepanel and top connector
    [side_panel.kicad_pcb, side_panel.kicad_sch, top_connector.kicad_pcb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]
2024-09-20 Test workflow using devcontainer
    [partition_table.csv, side_panel.kicad_pcb]
2024-09-20 set fetch depth in workflow
    [top_connector.kicad_pcb]
2024-10-03 Add FreeCad model and update board layout.
    [GA12-N20.stp, HLE-108-02-L-DV-BE-TR.stp, openflap_cad_model.FCStd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]
2024-10-11 Add script to exptort stl files from freecad
    [openflap_cad_model.FCStd]
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2024-10-23 create encoder wheel in kicad
    [encoder_wheel.brd, encoder_wheel_48.kicad_pcb, encoder_wheel_48.kicad_sch]
2024-10-23 update ci scripts to allow out of source builds
    [side_panel.kicad_pcb, top_connector.kicad_pcb]
2024-12-27 Remade controller hardware in KiCad.
    [DC_JACK_SMT.stp, GA12-N20.stp, HLE-108-02-L-DV-BE-TR.stp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]
2024-12-28 Added TVS diode to UART line on side pannel
    [controller.kicad_sch, side_panel.kicad_pcb, side_panel.kicad_sch]
2024-12-28 Fix CI ERC & DRC errors
    [controller.kicad_pcb, controller.kicad_sch, encoder_wheel_48.kicad_pcb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]
2024-12-28 Changed micro symbol to uF
    [controller.kicad_pcb, controller.kicad_sch]
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2024-12-29 hardware/resources/DC_JACK_SMT.stp: convert to Git LFS
    [DC_JACK_SMT.stp]
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2024-12-30 fixed color override in freecad model
    [openflap_cad_model.FCStd]
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2025-01-16 Reduce clearance between hub and core and increase mounting hole diameter plus add chamfer
    [openflap_cad_model.FCStd]
2025-01-16 offset encoder pattern so inner trace does not line up with fasteners
    [encoder_wheel_48.kicad_pcb, encoder_wheel_48.kicad_sch]
2025-01-16 reverse motor polarity on side pannel
    [side_panel.kicad_pcb, side_panel.kicad_sch]
2025-01-16 remove series resistors from uart lines on modules
    [side_panel.kicad_pcb, side_panel.kicad_sch]
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2025-01-26 fix: flip front and back of 3d printed flaps
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2025-01-29 reduce flap wheel side to side tolerance
    [openflap_cad_model.FCStd]
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2025-02-01 refactor: improve error handling and update message structures in chain communication
    [flap_uart.c, main.c]
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2025-02-01 reworking chain com message format
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2025-02-01 fix module chain com bug
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2025-02-01 fix chain com read all dynamic size not working for consecutive modules
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2025-02-01 move flap latch from 1 degree to 3.5 degrees
    [openflap_cad_model.FCStd]
2025-02-01 Add short backspin to align lock flap against the latch.
    [main.c]
2025-02-01 elongate flap retainer by 2mm and add mounting dove tail in the back
    [openflap_cad_model.FCStd]
2025-02-02 shrink top 0.5mm and reduce retainer thickness by .25mm
    [openflap_cad_model.FCStd]
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2025-02-18 Increase encoder LED current to 70mA and make make two pairs of 3 to reduce power draw
    [side_panel.kicad_pcb, side_panel.kicad_sch]
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2025-03-07 Side panel 5.0.1 swap motor polarity
    [side_panel.kicad_pcb, side_panel.kicad_sch]
2025-03-08 Change sidepanel IR resistor to 15ohm and finalize encoder wheel design
    [encoder_wheel_48.kicad_pcb, encoder_wheel_48.kicad_sch, side_panel.kicad_pcb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]
2025-03-08 Start homing on boot and prevent flippering between 1 and 0.
    [main.c]
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2025-03-27 increase hub and core CAD tolerances to reduce friction
    [openflap_cad_model.FCStd]
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2025-03-29 Fix module startup calibration.
    [main.c]
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2025-07-31 Rework top connector and side panel connections to increase power rating. Switch from 2 channel to 4 channel incremental encoder.
    [HLE-107-02-L-DV-BE-A-TR.stp, encoder_wheel_48.kicad_pcb, openflap_cad_model.FCStd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]
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2025-08-02 Update side panel to add proper ESD protection, 12V detection, removed uart switch in favor of software switching, shuffled around some IO for improved routing.
    [controller.kicad_pcb, controller.kicad_sch, side_panel.kicad_pcb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]
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2025-08-23 Rework firmware to work with v5.0.2 hardware.
    [main.c]
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2025-08-27 rework sidepanel to 3 sensors, ad 12V ok signal, add debug uart, change test points for skedd connector
    [side_panel.kicad_pcb, side_panel.kicad_sch]
2025-09-01 Fixed OTA, Added checksum to chain comm
    [main.c]
2025-09-01 Add onboard 3.3V regulator to side panal so that uart communication may switch to 3.3V
    [encoder_wheel_48.kicad_pcb, side_panel.kicad_pcb, side_panel.kicad_sch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]
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2025-09-11 Test PCB with 16 nodes for testing and debugging the communication protocol
    [ccn.kicad_sch, chaincom_test.kicad_pcb, chaincom_test.kicad_sch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]
2025-09-15 Fix synchronization issue between controller and modules
    [main.c]
2025-09-16 Fix issue causing calibration not to got to home position.
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2025-09-23 fix erroneous U4 angle from 45 to 37.5
    [side_panel.kicad_pcb, side_panel.kicad_sch]
2025-09-24 Add dynamic uart routing and bridging to controller, Remove OLED libs
    [controller.kicad_pcb, controller.kicad_sch, test_partition_table.csv]
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2025-10-15 Complete Redesign of Chain Communication Protocol
    [main.c]
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2025-10-16 Fixed compile errors in master but it's still shit.
    [test_partition_table.csv]
2025-10-21 Got cc master working for fw version prop
    [partition_table.csv, test_partition_table.csv]
2025-10-23 Bugfixes and testing, working module & controller
    [side_panel.kicad_pcb, side_panel.kicad_sch]
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2025-11-03 Add a command to reset/start the offset calibration
2025-11-04 Enhance chain communication with queuing mechanism and UART callbacks
    - Added queuing support for read and write actions in the chain communication master.
    - Introduced UART callback for waiting until transmission is complete.
    - Updated synchronization logic to handle retries for property synchronization.
    - Adjusted timeout values for improved responsiveness.
    - Enhanced error logging for better debugging of module errors.
    [openflap_cc_master.c, openflap_cc_master_uart.c]
2025-11-06 Fix return codes of module prop handlers
2025-11-10 Change barel jack for XT30 connector and bump LDO to 600mA, remove usb power switch in favor of diode.
    [XT30-M.STEP, controller.kicad_pcb, controller.kicad_sch]
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2025-11-12 Renamed "chain comm" to "madelink" and made it into a submodule
    [test_partition_table.csv]
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2026-05-27 Fix erroneous offset_delta calculation for offset calibration.
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
